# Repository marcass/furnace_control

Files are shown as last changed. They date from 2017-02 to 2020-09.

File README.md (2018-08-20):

# furnace_control
Control a FUWI pellet boiler with arduino to improve smarts

After having 2 controal boards malfunction I have decided to roll my own with some improved modulation of fan speed and pellet feeding. Reporting or interface issues will be addressed also

Goals satisfied with this project are (not limited to):
* Reducing the need for cleaning of pellet boiler through better end of heat cycle managemtn of burner box (basically fanning the pellet wad until it burns out)
* Increasing efficiency of pellet usage by varying energy output of pellet boilder in accordance with demand (pid controlling fan, pellet feed time and pause feed time around setpoint). This has the added benefit of avoiding short-cycling and resultant ash buildup

#Components of system
1. Pellet boiler
2. Sensor network for house (managed by https://github.com/home-climate-control/dz ) - this will pull a pin low on arduino in boiler
3. Arduino controlled PCB in boiler
4. Communicatons server (communicates to arduino via usb-serial port and the rest of the world via MQTT)

This repository deals with the arduino sketch, the PCB and the communication interface on the server

# To perform headless-server update of arduino sketch
1. Stop python listener script on serial port "sudo systemctl stop arduino-attach.service"
2. Upload script to arduino: "make upload" (in root of git repo for furnace_control)
3. Start python listener script on serial port: "sudo systemctl start arduino-attach.service"

## Inputs from boiler
* Water temperature
* Auger shaft temperature
* Light sensor in flame box

## Outputs to boiler and assocaited hardware
* Auger motor to move pellets into flame box
* Fan to stoke fire
* 280W eleement to start fire
* Circ pump to pump heated water to radiators

## Safety
Hardware fail-safes are ideal as software may have problems that result in uncontrolled fire! Currently the boiler uses a device that breaks the neutral feed to the fan and element so it does not provide continuance when it is over a certain termperature (90 degrees C)
 * Error state pulls all relays to low
 * Idle state pulls fan and element to low

## States
1. Idle
2. Start_up
3. Heating
4. Cool_down
5. Error
6. Off

### Idle
 Wait for closed contact from 1-wire bus to transition into start_up. When contact closed: Blow fan to see if flame detected:
* if flame detected -> Heating
* if no flame -> Start_up

### Start up
1. Blow fan first to see if a flame will start
1. Pellet dump to get something for element to light
2. Element heating of pellet load
3. Gentle fan (phase angled to 30% or so) to start fire until light over threshold sensed
4. Pellet feed and full fan when light over threshold
5. Transition into heating when water temp over 50C

### Heating
1. PID control of trend of water temp and this affects fan speed through PWM and pellet feed rate
2. Start circ pump if over 50C
3. Pull fan relay low and circ pump high if temp over 85C
4. Transition to cool down if contact from 1-wire is opened

### Cool_down
1. Pull fan low and circ pump high until temp <60C
2. Transition to idle when below 60C

### Error
 Catch all that pulls fan adn element low

### Off
Don't start the boiler even if dz asks (button press and remote)

##Links
* Triac schematic for fan control (need up to 5A as heat diminishes capability
https://www.circuitar.com/media/product/25/files/Triac_v1.0.pdf

* Phase control for fan:
http://playground.arduino.cc/Main/ACPhaseControl
* ACPWM lib
http://playground.arduino.cc/Code/ACPWM
* Phase control explanation with varying of power output suggestions: http://electronics.stackexchange.com/questions/19273/when-should-i-fire-the-triacs-gate-when-controlling-an-inductive-load-ac-motor

##Connecton notes
* redundant fan_out connection at relay block in case on-board pahse angle not working
* P6 (240v outs) have the hardware thermostat (AB03 90.05) connected in pins 3 and 4 (polarity doesn't matter
  * when below 90C it is closed circuit
  * when above 90C it is open circuit
  * after opening it closes again at 75C
  * this (when closed circuit) supplies 240N to pins 1, 2 and 3 (pump, auger and element)
* 1-wire relay (hobby boards 8 channel) connects at pins 7 and 8 of P1 (low voltage input connector). When it is closed by control software the DZ_pin is pulled to ground
* 15k Ohm resistors need to be rated for 5w on 240VAC side (consumes 3.8W of power)
* 1.5k Resistor needs to be 50W on 240VAC side (consumes 38W of power) if constant power, but as MOC305 datasheet states:

"The power dissapation of this current limiting resistor and the triac driver is very small because the power triac carris the load current as soon as the current through the driver and current limiting resistor reaches the trigger current of teh power triac"

Switching times for the driver are 1 micro second and 4 micro seconds for the power triac

#Setup
Components of the sytsem are:
1. Boiler controller (arduino based on a PCB)
2. Communication interface on serial port
3. Display device(s)

##Boiler controller
PCB in kicad files in this repo
* Could do with 2 additional input pins for sensing hopper level
* Check that 5W resistors are up to the task of phase angle detection

## Communication interface on serial port
Uses:
* pyserial to capture data/print data to serial port (arduino) and insert into database
* paho-mqtt for subscribing/publishing to mosquitto broker
* mosquitto broker for managing infomration

###UDEV
See udev rules in repo:
* On insertion of aruduino usb assign symlink so pyserial can find device
* runs systemd service that starts the pythion script for managing stuff to and from arduino

###Data capture
Inserting data into influxdb and graphing via a vuejs frontend using plotly. See https://skibo.duckdns.org/sensors/#/graphs (repo here: https://github.com/marcass/esp32-sensornet/tree/master/sensornet)

##Device
Any mqtt client that runs on anything will display data from broker
* subscribe to topics:
  * boiler/switch (for turning on/off)
  * boiler/flame (for displaying flame value)
  * boiler/temp/auger
  * boiler/temp/water
  * boiler/temp/setpoint
  * boiler/messages (error messages)
  * boiler/state (state display)

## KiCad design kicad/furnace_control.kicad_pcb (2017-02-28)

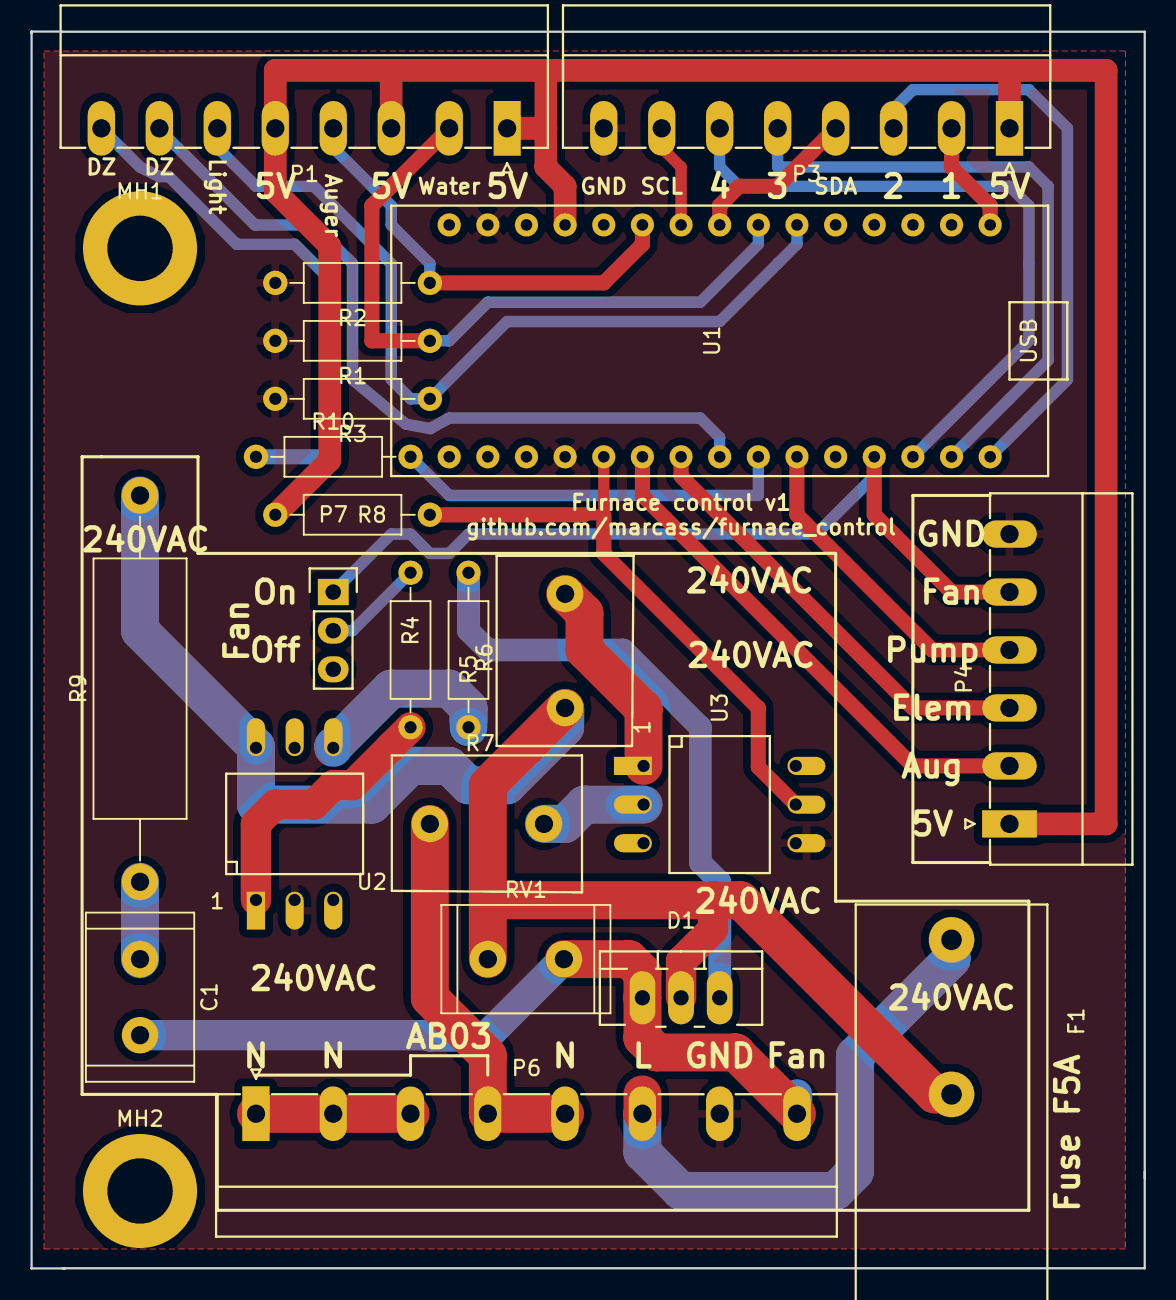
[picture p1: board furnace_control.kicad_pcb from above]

Board: 2 copper layers, 73.2 x 81.3 mm, 24 parts (0 on the bottom side), 31 nets.

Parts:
C1: 0.01muF; R_Radial_Power_L11.0mm_W7.0mm_P5.00mm
D1: Q6015L5; TO-220_Neutral123_Vertical_LargePads
F1: Fuse; Fuseholder5x20_Horizontal_closed_Bulgin_FX0457
MH1, MH2: Mounting_hole; MountingHole_4.3mm_M4_DIN965_Pad
P1: CONN_01X08; PhoenixContact_MC-G_08x3.81mm_Angled
P3: LCD_Button; PhoenixContact_MC-G_08x3.81mm_Angled
P4: CONN_01X06; PhoenixContact_MC-G_06x3.81mm_Angled
P6: 240_CONN_Therm_on_3_4; PhoenixContact_MC-G_08x5.08mm_Angled
P7: Jumper; Pin_Header_Straight_1x03
R1, R2, R3, R8: 10k; R_Axial_DIN0207_L6.3mm_D2.5mm_P10.16mm_Horizontal
R4, R10: 220; R_Axial_DIN0207_L6.3mm_D2.5mm_P10.16mm_Horizontal
R5: 1.5k; R_Axial_DIN0207_L6.3mm_D2.5mm_P10.16mm_Horizontal
R6, R7: 15K; Resistor_5W_l12.5_w9_P7.5
R9: 33; R_Axial_DIN0617_L17.0mm_D6.0mm_P25.40mm_Horizontal
RV1: Varistor 600V; R_Radial_Power_L11.0mm_W7.0mm_P5.00mm
U1: arduino_nano; ArduinoNano
U2: MOC3052M; Optocoupler_6pin_wide_Stile-I
U3: H11AA1; Optocoupler_6pin_wide_Stile-I

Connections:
+5V: P1.1, P1.3, P1.5, P3.1, P4.1, R8.1, U1.12
/N: P6.1, P6.2, P6.3
/Neutral: P6.4, P6.5, R7.1
Button_1: P3.2, U1.1
Button_2: P3.3, U1.30
Button_3: P3.5, U1.29
Button_4: P3.6, U1.28
GND: P3.8, P4.6, P6.7, R1.2, R2.2, R3.2, U1.14, U1.19, U2.2, U3.4
unnamed: C1.1, R9.1
unnamed: C1.2, D1.1, P6.8, RV1.2
unnamed: D1.2, F1.2, R6.1, R9.2, RV1.1, U2.6
unnamed: D1.3, R5.1
unnamed: F1.1, P6.6
unnamed: P1.8, R10.1
unnamed: P7.2, R4.2
unnamed: R4.1, U2.1
unnamed: R5.2, U2.4
unnamed: R6.2, U3.1
unnamed: R7.2, U3.2
Out_auger: P4.2, U1.21
SCL: P3.7, U1.9
SDA: P3.4, U1.8
ac_in: R8.2, U1.20, U3.5
auger_temp: P1.4, R2.1, U1.10
dz_pin: P1.7, U1.23
dz_supply: R10.2, U1.24
element: P4.3, U1.22
fan_out: P4.5, P7.1, U1.27
light: P1.6, R3.1, U1.6
pump: P4.4, U1.25
water_temp: P1.2, R1.1, U1.7

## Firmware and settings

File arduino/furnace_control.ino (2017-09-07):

/* ToDo
 *  - check lcd working
 *  - put ultrasound probe on analoge pins (as digital?)
 */

/*******************************
 BOILER CONTROL
 *******************************/
//#define debug
#define pid //use if PID controlling fan output
//#define no_PID //use if not pid controlling
#define mqtt
//#define ac_counter
//#define lcd //interferes with interrupts?

//Libraries
//#include <Wire.h>
//#ifdef lcd
//  //https://bitbucket.org/fmalpartida/new-liquidcrystal/wiki/Home
//  #include <LiquidCrystal_I2C.h>
//  LiquidCrystal_I2C lcd(0x27, 2, 1, 0, 4, 5, 6, 7, 3, POSITIVE);  // Set the LCD I2C address
////need to set contrast and backlight and check pin assignments
//#endif
//PID library
#include <math.h>
#include <PID_v1.h>
//for ac phase angle stuff
#include <avr/io.h>
#include <avr/interrupt.h>
#include "FastRunningMedian.h" //for getting flame val median http://forum.arduino.cc/index.php?topic=53081.msg1160999#msg1160999

/*******************************************************************************
 * Constants
 */
//timers
unsigned long ELEMENT_TIME = 450000; //7.5min in ms
unsigned long START_FEED_TIME = 120000; //2min in ms for pellet feed initially
unsigned long SUBSEQUENT_START_FEED_TIME = 5000; //little top up of pellets if not starting first time
unsigned long START_FAN_TIME = 120000; //2min in ms for time to blow to see if flame present
//const long DUMP_START = 45000;//45s of fanning before throwing a little fuel on the fire
unsigned long END_FAN_TIME = 600000; //10min of blow to empty puck from burn box
unsigned long PUMP_TIME = 30000; //30s in ms to avoid short cycling pump
unsigned int BUTTON_ON_THRESHOLD = 1500;//1.5s in ms for turning from off to idle and vice versa
unsigned long FEED_PAUSE = 24000; //60s and calculating a result so might need to be a float
unsigned long FEED_TIME = 10000;//default pellet feed time
unsigned long STATE_CHANGE_THRES = 5000;//time that needs to elapse before changing STATE_START_UP <- STATE_HEATING
unsigned long STATE_CHANGE_THRES_UP = 2000;//time that needs to elapse before changing STATE_START_UP -> STATE_HEATING
unsigned long STOP_THRESH = 5000; //for  fan short cycling
unsigned long ERROR_THRES = 5000;//time that must elapse before goes into error at startup (not working at present)
unsigned long RESET_THRESHOLD = 300000; //time that must elapse before start count gets reset
unsigned int FLAME_READ_INTERVAL = 30; //read flame val every 30ms to build array for calculating average value (smoothing)
//temps
const int LOW_TEMP = 50; //deg C -> low end of heating range
const int HIGH_TEMP = 75; //deg C -> high end of heating range
const int MID_TEMP = 63;//Send back to heating if over heats from here
const int TOO_HOT_TEMP = 85; //cool down NOW
const int AUGER_OVER_TEMP = 45; //deg C - don't want a hopper fire
//flame values
const int FLAME_VAL_THRESHOLD = 120;//work out a value here that is reasonable
const int START_FLAME = 50;
//States
const int STATE_IDLE = 0;
const int STATE_START_UP = 1;
const int STATE_HEATING = 2;
const int STATE_COOL_DOWN = 3;
const int STATE_ERROR = 4;
const int STATE_OFF = 5;
//Buttons (numbers from left
const int BUTTON_1 = 13;
const int BUTTON_2 = 12;
const int BUTTON_3 = 11;
const int BUTTON_4 = 10;
//Outputs
const int PUMP = 7; //circ pump relay
const int FAN = 9; //fan relay. pin9 is a PWM pin and allows for analogWrite
const int AUGER = 3; //pellet auger relay
const int ELEMENT = 4; //fire starting element relay
//Inputs
const int WATER_TEMP = 3; //analogue pin 3
const int AUGER_TEMP = 6; //analogue pin 6
const int LIGHT = 2; //analogue pin 2 for flame detection
const int DZ_PIN = 5; // pin that is pulled up when 1-wire relay closes
const int DZ_SUPPLY = 6; //Need a pin to supply 5v that is passed to DZ_PIN when 1-wire relay closes
#define DETECT 2 //ac detection pin
#define GATE 9 //pwm pin
#define PULSE 4   //trigger pulse width (counts) that triac requires to fire one specified needs ~25mus

/********************************************************************************************
 * Variables
 */ 
// general timers (specific ones in subsection)
unsigned long debounce_start = 0; //button press debounce
unsigned long element_start = 0;
unsigned long fan_start = 0;
unsigned long fanend_start = 0;
unsigned long auger_start = 0;
unsigned long reset_dump_count;
unsigned long state_trans_start = 0;
unsigned long state_trans_stop = 0;
unsigned long stop_start = 0; //for  fan short cycling
unsigned long start_feed_time = 0;//pellets
unsigned long start_feed_pause = 0;//pellets
unsigned long start_pump_time = 0;//pump short cycling
int on_wait; //variable for converting power to timer value
unsigned long feed_pause;//var for pellets puase time
unsigned long feed_time;//var for feed time
//sensor readings
int auger_temp;
int flame_val; // range from 0 to 1024 ( i think)
//counters
int start_count = 0;
int crosses;
int counts;
int dump_count = 0;//counter to make sure we don't fill up chamber with pellets
//tests
bool reset = false;
bool feeding = true;
bool cooling = false;
bool dump = false;
bool elem = false;
bool blowing = false;
//maths
int proportion;
float divisor;
//state stuff
String reason = "";
int state;
int this_state;
//reading flame value stuff and smoothing
FastRunningMedian<int, 32, 1> newMedian;
// Constructor: 
// FastRunningMedian<datatype_of_content, size_of_sliding_window, default_value> 
// maximim size_of_sliding_window is 255
// Methods:
// addValue(val) adds a new value to the buffers (and kicks the oldest)
// getMedian() returns the current median value
unsigned long prevMillis;
//const int numReadings = 10;
//int readings[numReadings];      // the readings from the light sensor
//int readIndex = 0;              // the index of the current reading
//int total = 0;

/****************************************************************************************
 * PID
 */
#ifdef pid
  double Kp=10, Ki=0.001, Kd=1; //P, I and D see http://playground.arduino.cc/Code/PIDLibrarySetTunings
  double temp_set_point = 63; //PID temp SETPOINT
  double power; //variable for percentage power we want fan to run at works from 30 (min) to 80 (max)
  double water_temp;
  double feed_pause_percent;
  double feed_percent;
  //PID fanPID(&Input, &Output, &Setpoint,2,5,1, DIRECT);
  PID fanPID(&water_temp, &power, &temp_set_point,Kp, Ki, Kd, DIRECT); //need more fan power to get hotter so DIRECT
  PID pausePID(&water_temp, &feed_pause_percent, &temp_set_point,Kp, Ki, Kd, REVERSE); //need shorter feed time to get to hotter so REVERSE
  PID feedPID(&water_temp, &feed_percent, &temp_set_point,Kp, Ki, Kd, DIRECT);
  /* maths  may need to be addedfor value calcs (pid outputs value of 0-255 and we want to convert to 
   *  range in percentage limits
   *  http://playground.arduino.cc/Code/PIDLibrarySetOutputLimits states that 
   *  feedPID.SetOutputLimits(40,100); should alter default behavior, but I wonder if it is a trncater version
   *  of 0-255
   *  - fan runs at 30-80% of power (phase angle control fails outside that range)
   *  - pellets feed I want to run at 40-100% of time in range
   *  - pause I want to run between 60-100% of time in range
   */
#endif

#ifdef no_PID
  int power; //variable for percentage power we want fan to run at works from 30 (min) to 80 (max)
  int water_temp; 
#endif

//MQTT *****************************************************************************************

#ifdef mqtt
  long PUB_INTERVAL = 1000; //1 second to cylce between publishing events while running
  long previousMillis = 0;
  const long PUB_INTERVAL_IDLE = 30000; //publish state info and temp info for logging while not running
  int index = 0; //counter for cycling through publishing array
  //topics
  int fan_power; //what fan is actually running at
  String STATE_TOPIC = "boiler/state";
  String WATER_TEMP_TOPIC = "boiler/temp/water";
  String AUGER_TEMP_TOPIC = "boiler/temp/auger";
  String FLAME_TOPIC = "boiler/flame";
  String ERROR_TOPIC = "boiler/messages";
  String PID_FAN = "boiler/pid/fan";
  String PID_FEED = "boiler/pid/feed";
  String PID_PAUSE = "boiler/pid/pause";
  String START_COUNT_TOP = "boiler/start_count";
  String TEMP_SET_POINT_TOP = "boiler/temp/setpoint";
  const String STATES_STRING[] = {"Idle","Starting","Heating","Cool down","Error","Off","Wind down"};
  
  //publish functions overloaded for int/string as payload
  void publish(String top,int payload) { //publish data
    Serial.print("MQTT:");
    Serial.print(top);
    Serial.print("/");
    Serial.println(payload);
  }
  void publish(String top,String payload) { //publish data
    Serial.print("MQTT:");
    Serial.print(top);
    Serial.print("/");
    Serial.println(payload);
  } 
#endif

// SETUP SERIAL COMM for inputs *********************************************************
String inputString = "";         // a string to hold incoming data
boolean stringComplete = false;  // whether the string is complete

void serialEvent() {
  while (Serial.available()) {
    // get the new byte:
    char inChar = (char)Serial.read();  // add it to the inputString:
    inputString += inChar;
    if (inChar == '\n') {
      stringComplete = true;
    } 
  }
}

//phase angle interrupts ***************************************************************
void zeroCrossingInterrupt(){ //zero cross detect   
  TCCR1B=0x04; //start timer with divide by 256 input
  TCNT1 = 0;   //reset timer - count from zero
  crosses++;
}

ISR(TIMER1_COMPA_vect){ //comparator match
  digitalWrite(GATE,HIGH);  //set TRIAC gate to high
  TCNT1 = 65536-PULSE;      //trigger pulse width
}

ISR(TIMER1_OVF_vect){ //timer1 overflow
  digitalWrite(GATE,LOW); //turn off TRIAC gate
  TCCR1B = 0x00;          //disable timer stopd unintended triggers
}

//Analogue reading maths for temp ******************************************************
double Thermistor(int RawADC) {
 double Temp;
 Temp = log(10000.0*((1024.0/RawADC-1)));
 //         =log(10000.0/(1024.0/RawADC-1)) // for pull-up configuration
 Temp = 1 / (0.001129148 + (0.000234125 + (0.0000000876741 * Temp * Temp ))* Temp );
 Temp = Temp - 273.15;            // Convert Kelvin to Celcius
 //Temp = (Temp * 9.0)/ 5.0 + 32.0; // Convert Celcius to Fahrenheit
 return Temp;
}


void setup() {
  //intitialise output pins (inputs are all analogue read pins)
  pinMode(DETECT, INPUT);     //zero cross detect
  digitalWrite(DETECT, HIGH); //enable pull-up resistor
  pinMode(GATE, OUTPUT);      //TRIAC gate control
  digitalWrite(GATE, LOW);
  pinMode(PUMP, OUTPUT);
  digitalWrite(PUMP, LOW);
  pinMode(FAN, OUTPUT);
  digitalWrite(FAN, LOW);
  pinMode(AUGER, OUTPUT);
  digitalWrite(AUGER, LOW);
  pinMode(ELEMENT, OUTPUT);
  digitalWrite(ELEMENT, LOW);
  pinMode(DZ_SUPPLY, OUTPUT);
  digitalWrite(DZ_SUPPLY, LOW);
  //digitalWrite(A2, LOW);
  //Initialise inputs
  pinMode(DZ_PIN, INPUT_PULLUP);
  pinMode(BUTTON_1, INPUT_PULLUP);
  pinMode(BUTTON_2, INPUT_PULLUP);
  pinMode(BUTTON_3, INPUT_PULLUP);
  pinMode(BUTTON_4, INPUT_PULLUP);
  #ifdef pid
    //initialize the PID variables we're linked to
    fanPID.SetOutputLimits(30, 80); //percentage of fan power
    fanPID.SetSampleTime(3000); //SAMPLES EVERY 3s
    pausePID.SetOutputLimits(100, 170); //percentage of feed time check to see that burning all of load
    pausePID.SetSampleTime(3000);
    feedPID.SetOutputLimits(60,100); //percentage of feed time check to see that burning all of load
    feedPID.SetSampleTime(3000);
    //turn the PID on
    fanPID.SetMode(AUTOMATIC);
    pausePID.SetMode(AUTOMATIC);
    feedPID.SetMode(AUTOMATIC);
  #endif
  // set up Timer1 
  //(see ATMEGA 328 data sheet pg 134 for more details)
  OCR1A = 100;      //initialize the comparator
  TIMSK1 = 0x03;    //enable comparator A and overflow interrupts
  TCCR1A = 0x00;    //timer control registers set for
  TCCR1B = 0x00;    //normal operation, timer disabled
  // set up zero crossing interrupt
  attachInterrupt(0,zeroCrossingInterrupt, RISING); //IRQ0 is pin 2. Call zeroCrossingInterrupt 
  // initialize serial communication:
  Serial.begin(9600);//slower speed for long cable
  inputString.reserve(200); // reserve mem for received message on serial port 
  int state = 0;
  #ifdef mqtt
    //initialise state as idle on statup
    Serial.print("MQTT:");
    Serial.print(STATE_TOPIC);
    Serial.print("/");
    Serial.println(STATES_STRING[state]);
  #endif
}

//Functions that do stuff ********************************************************************
void fan(bool runFan, int x) {
  #ifdef mqtt
    fan_power = x;
  #endif
  if (!runFan) {
    digitalWrite(GATE,LOW);
    //undo phase angle magic here 
    TCCR1B = 0x00;
    TIMSK1 = 0x00;    //disable comparator A and overflow interrupts
    TCCR1A = 0x00;    //timer control registers set for
    TCCR1B = 0x00;    //normal operation, timer disabled
    stop_start = 0;
    power = 0;
  }
  if (runFan) {
    #ifdef debug
      Serial.print(" FAN ON at ");
      Serial.print(x);
    #endif
    if (x == 100) { //no phase angle control needed if you want balls out fan speed
      digitalWrite(GATE,HIGH);
    }else {
      //do magic phase angle stuff here
      /* x is the int as a percentage of fan power
       * OCR1A is the comparator for the phase angle cut-off
       * - when TCNT1 > OCR1A, ISR(TIMER1_OVF_vect) is called tellng optocoupler to power down
       * - 520 counts (16000000 cycles scaled to 256) per half AC sine wave @60hz (i think we run at 50Hz)
       * - fan stops over 80% of power, presumably latching the triac confusion over next zero cross => less than 156 count delay
       * - 30% is the lower power limit to avoid firing the triac too close to teh zero cross => delay not more than 364 count delay
       * - The smaller the value of OCR1A the more power we have
       */
      TIMSK1 = 0x03;    //enable comparator A and overflow interrupts
      //set up interrupt
      
      //attachInterrupt(0,zeroCrossingInterrupt, RISING);  // inturrupt 0 on digital pin 2
      
      //set a value that is a proportion of 520 for power
      divisor = (float)x / 100;
      proportion = divisor * 520;
      on_wait = 520 - proportion;
      if ( on_wait < 104) {
        OCR1A = 104;
      }
      if ( on_wait > 364) {
        OCR1A = 364;
      }else {
        OCR1A = on_wait;
      }
    }
  }
}

void pump(bool on) { //prevents short cycling of pump
  #ifdef debug
    Serial.print(" Pump: ");
    Serial.print(on);
  #endif 
  if (on) {
    digitalWrite(PUMP, HIGH);
    if (start_pump_time == 0) {    //avoid short cycling so pump for at least 30s
      start_pump_time = millis();
    }
  }
  if (!on) {
    if ( (millis() - start_pump_time) > PUMP_TIME) {
      digitalWrite(PUMP, LOW);
      start_pump_time = 0;
    }
  }
}

void flame_value_median() {
  unsigned long currentMillis = millis();
  if(currentMillis - prevMillis > FLAME_READ_INTERVAL) { 
    prevMillis = currentMillis; 
    newMedian.addValue(analogRead(LIGHT));
    flame_val = newMedian.getMedian();
  }
}


void fan_and_pellet_management() {
  //water temp measured in safety()
  //FAN MANAGEMENT
  if (water_temp < LOW_TEMP) { //go hard on the fan
    fan(true, 100);
  }else if (water_temp > HIGH_TEMP) {
    this_state = STATE_HEATING;
    state = STATE_COOL_DOWN;
    #ifdef mqtt
      //
      publish(STATE_TOPIC, STATES_STRING[state]);
    #endif    
  }else {
    #ifdef no_PID
      power = 75; //arbitrary value
    #endif
    fan(true, (int)power);
  }
  //PELLETS MANAGEMENT
  #ifdef pid
    feed_pause = (feed_pause_percent / 100) * FEED_PAUSE; //caluclate actual pause from PID derived value
    feed_time =  (feed_percent / 100)       * FEED_TIME;
  #endif
  #ifdef no_PID //won't be changing so set to const int value
    feed_time = FEED_TIME;
    feed_pause = FEED_PAUSE;
  #endif
  if (feeding) {
    if (start_feed_time == 0) {
      start_feed_time = millis();
    }
    //test to see if feed been on for long enough
    if ( (millis() - start_feed_time) > feed_time) {
      //stop feeding and start pausing
      feeding = false;
      start_feed_time = 0;
      //start_feed_pause = millis();
      digitalWrite(AUGER, LOW);
      #ifdef debug
        Serial.print("  Auger off  ");
      #endif
    }else {
      digitalWrite(AUGER, HIGH);
      #ifdef debug
        Serial.print("  Auger on  ");
      #endif 
    }
  } 
  if (!feeding) { 
    if (start_feed_pause == 0 ) {
      start_feed_pause = millis();
    }
    if ( (millis() - start_feed_pause) > feed_pause) {
      //stop pausing, start feeding
      
      start_feed_pause = 0;
      feeding = true;
    }
  }
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
void loop() {
  #ifdef debug
    Serial.print(" Sensors: ");
    Serial.print("W = ");
    Serial.print(water_temp);
    Serial.print(" A = ");
    Serial.print(auger_temp);
    Serial.print(" F = ");
    Serial.print(flame_val);
    Serial.print("State = ");
    Serial.println(STATES_STRING[state]);
  #endif 
  //***************   safety  *********************
  safety();
  //*************  see if we need to turn on or off  **************
  //get flame_val average
  flame_value_median();
  //dz calls it: 1-wire relay gets closed by DZ3
  if (digitalRead(DZ_PIN) == HIGH) {
    if ((state == STATE_HEATING) || (state == STATE_START_UP)) {
      fanend_start = 0;//not going for end fan time so trying to reset variable here
      this_state = STATE_IDLE;
      state = STATE_COOL_DOWN;
      #ifdef mqtt
        //
        publish(STATE_TOPIC, STATES_STRING[state]);
      #endif  
    }
  }
  //button press?
//  if (digitalRead(BUTTON_1) == HIGH) {
//    if (debounce_start == 0) {
//      debounce_start = millis();
//    }
//    if ( (millis() - debounce_start) > BUTTON_ON_THRESHOLD) {
//      if (state != STATE_OFF) {
//        state = STATE_IDLE;
//        #ifdef mqtt
//          //
//          publish(STATE_TOPIC, STATES_STRING[state]);
//        #endif        
//      }else {
//        state = STATE_OFF;
//        #ifdef mqtt
//          //
//          publish(STATE_TOPIC, STATES_STRING[state]);
//        #endif        
//      }
//      debounce_start = 0;
//    }else if (digitalRead(BUTTON_1) == LOW) { //button not held long enough so don't turn switch state and reset counter
//      debounce_start = 0;
//    }
//  }
  //serial instruction
  if (stringComplete) {
    if (inputString.startsWith("Turn Off Boiler")) {
      inputString = "";
      //reason = "";
      stringComplete = false;
      if ((state == STATE_IDLE) or (state == STATE_OFF) or (state == STATE_ERROR)){
        state = STATE_OFF;
      }else{
        this_state = STATE_OFF;
        state = STATE_COOL_DOWN;
      }
      #ifdef mqtt
        publish(STATE_TOPIC, STATES_STRING[state]);
      #endif
    }
    if (inputString.startsWith("Turn On Boiler")) {
      inputString = "";
      stringComplete = false;
      state = STATE_IDLE;
      #ifdef mqtt
        publish(STATE_TOPIC, STATES_STRING[state]);
      #endif
//      reason = "";
//      #ifdef mqtt
//        //
//        publish(ERROR_TOPIC, reason); //clear error register
//      #endif    
      start_count = 0;  
      //delay(10);
    }else if (inputString.startsWith("Increase SetPoint")) {
      inputString = "";
      stringComplete = false;
      if (temp_set_point < 73){
      (int)temp_set_point++; 
      publish(TEMP_SET_POINT_TOP, temp_set_point);     
      }
      

    }else if (inputString.startsWith("Decrease SetPoint")) {
      inputString = "";
      stringComplete = false;
      if (temp_set_point > 60){
        (int)temp_set_point--;
        publish(TEMP_SET_POINT_TOP, temp_set_point);
      }
      
    }
  }
  
  switch (state) {
    case STATE_IDLE:
      proc_idle();
      break;
    case STATE_START_UP:
      proc_start_up();
      break;
    case STATE_HEATING:
      proc_heating();
      break;
    case STATE_COOL_DOWN:
      proc_cool_down(this_state);
      break;
    case STATE_ERROR:
      proc_error();
      break;
     case STATE_OFF:
      proc_off();
      break;
  }
  if (stringComplete){
    inputString = "";
    stringComplete = false;
  }
  #ifdef mqtt
    if ((state == STATE_START_UP) or (state == STATE_HEATING) or (state == STATE_COOL_DOWN)) { //publishs
      int mosqPayload[] = {water_temp, auger_temp, flame_val, state, fan_power, feed_percent, feed_pause_percent, temp_set_point};
      const String mosqTop[] = {WATER_TEMP_TOPIC, AUGER_TEMP_TOPIC, FLAME_TOPIC, STATE_TOPIC, PID_FAN, PID_FEED, PID_PAUSE, TEMP_SET_POINT_TOP};
      //publish everything in a round robin fashion
      if(millis() - previousMillis > PUB_INTERVAL) { //publish info
        previousMillis = millis();  
        if (index < 7 ) {
          index++; 
        }else {
          index = 0;
        }
        if (index==3){
         publish(mosqTop[index], STATES_STRING[state]);
        }else{
          publish(mosqTop[index], mosqPayload[index]);
        }
      }
    }else { //publish temp, pause for PUB_INTERVAL_IDLE, publish state, pause for PUB_INTERVAL_IDLE, publish temp etc
      if (index > 1) {//set it to value for publishing if was in higher value from prev on state
        index = 0;
      }
      if( (millis() - previousMillis) > PUB_INTERVAL_IDLE) { //publish info
        previousMillis = millis();
        if (index < 1) { 
          publish(WATER_TEMP_TOPIC, water_temp);//water temp in first member of arrays
          index++;
        }
        if (index == 1) {
          publish(STATE_TOPIC, STATES_STRING[state]);
//          if (state == STATE_ERROR) {
//            publish(ERROR_TOPIC, reason);
//          }
          index = 0;
        }
      }
        
    }

  #endif
  #ifdef ac_counter
    if (crosses > 60) {
      crosses = 0;
      counts++;
      Serial.print("Number of counts = ");
      Serial.println(counts);
    }
  #endif
  //delay(200); //can't read form serial with delay
}

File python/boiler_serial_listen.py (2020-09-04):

import serial
import time
# import boiler_alerts as alerts
import creds
import paho.mqtt.client as mqtt
import paho.mqtt.publish as publish
import requests
import creds
import json
from threading import Thread

AUTH_URL = 'https://skibo.duckdns.org/api/auth/login'
DATA_URL = 'https://skibo.duckdns.org/api/data'
headers = ''
jwt = ''

# dict of topics for messaging
boiler_topics = {"boiler/state":"State", "boiler/temp/water":"Water temp", "boiler/temp/auger": "Auger temp", "boiler/temp/setpoint": "Setpoint"}
boiler_data = {'State': '', 'Water temp': 0, 'Auger temp': 0, 'Setpoint': 0}
state_arr = ['Idle', 'Starting', 'Heating', 'Cooling', 'Error', 'Off']

def getToken():
    global jwt
    global headers
    r = requests.post(AUTH_URL, json = {'username': creds.user, 'password': creds.password})
    tokens = r.json()
    #print 'token data is: ' +str(tokens)
    try:
        jwt = tokens['access_token']
        headers = {"Authorization":"Bearer %s" %jwt}
    except:
        print ('oops, no token for you')

def post_data(data):
    global jwt
    global headers
    if (jwt == ''):
        print ('Getting token')
        getToken()
    ret = requests.post(DATA_URL, json = data, headers = headers)
    #print 'JWT = '+str(jwt)
    #print 'First response is: ' +str(ret)
    if '200' not in str(ret):
        print ('Oops, not authenticated')
        try:
            getToken()
            requests.post(DATA_URL, json = data, headers = headersi)
            ret = {'Status': 'Error', 'Message': 'Got token'}
            print ('Post NOT 200 response is: ' +str(r))
        except:
            ret =  {'Status': 'Error', 'Message': 'Failed ot get token, so cannot perform request'}
    #print ret
    #return ret.json()

# The callback for when the client receives a CONNACK response from the server.
def on_connect(client, userdata, flags, rc):
    print("Connected with result code "+str(rc))
    # Subscribing in on_connect() means that if we lose the connection and
    # reconnect then subscriptions will be renewed.
    client.subscribe("boiler/#")

# The callback for when a PUBLISH message is received from the server.
def on_message(client, userdata, msg):
    message = str(msg.payload, 'UTF-8')
    if 'switch' in msg.topic:
        #print ("port write request received")
        #print(message)
        if ('Setpoint' in message) or ('State'  in message):
            port.write('\r\n'+message+'\r')
            print ('Sent ' + message + ' to serial port.')
    allowed_passthrough_msg = ['Turn Off Boiler', 'Turn On Boiler', 'Increase SetPoint', 'Decrease SetPoint']
    if message in allowed_passthrough_msg:
        #print ("Message allowed through")
        to_send = ('\r\n'+message+'\r\n').encode()
        port.write(to_send)
        #port.write(('\r\n'+message+'\n\r').encode())
        #port.write('\r\n')
        #port.write(message)
        #port.write('\r')
        #print ('Sent ' + message + ' to serial port.')

def parse_packet(payload, sensor):
    #payload = str(payload, 'UTF-8')
    #print(sensor, payload)
    try:
        if 'temp' in sensor:
            temp_type = sensor.split('/')[-1:][0]
            #print ('temp type is: '+str(temp_type)+', value is: '+payload)
            #data.write_data(temp_type, 'temperature', int(payload))
            packet = {'tags': {'state':boiler_data['State'], 'type':'temp', 'sensorID':temp_type, 'site': 'boiler'}, 'value':float(payload), 'measurement': 'things'}
        if 'state' in sensor:
            state = int(payload)
            # Publish string value to state
            readable_state = state_arr[state]
            boiler_data['State'] = readable_state
            client.publish('boiler/state/readable/', readable_state, 0, True)
            packet = {'tags': {'state':boiler_data['State'], 'type':'state', 'sensorID':'state', 'site': 'boiler'}, 'value':state, 'measurement': 'things'}
        if 'pid' in sensor:
            pid_type = sensor.split('/')[-1:][0]
            pids = ['fan', 'pause', 'feed']
            if pid_type in pids:
                # data.write_data(pid_type, 'pid', int(payload))
                packet = {'tags': {'state':boiler_data['State'], 'type':'pid', 'sensorID':pid_type, 'site': 'boiler'}, 'value':int(payload), 'measurement': 'things'}
            else:
                print('Mangled PID typ')
        if 'flame' in sensor:
            # data.write_data('burn', 'flame', int(payload))
            packet = {'tags': {'state':boiler_data['State'], 'type':'light', 'sensorID':'flame', 'site': 'boiler'}, 'value':int(payload), 'measurement': 'things'}
        #print(packet)
        return packet
    except:
        packet = 0
        return packet


def write_setpoint(setpoint):
    port.write('\r\n'+'Setpoint'+'['+setpoint+']'+'\r')
    print ('Sent Setpoint[' + setpoint + '] to serial port.')

def write_state(state):
    # "Idle","Starting","Heating","Cool down","Error","Off"
    port.write('\r\n'+'State'+'['+state+']'+'\r')
    print ('Sent State[' + state + '] to serial port.')

def readlineCR(port):
    global boiler_data
    global client
    rv = ""
    while True:
        ch = port.read()
#        print(ch)
#        rv += ch
#       for python3 need to cast to str
        try:
            rv += str(ch, 'UTF-8')
        except:
            print('Serial character decoding error')
            pass
#        rv += str(ch)
#        print(rv)
        if ch==b'\r':# or ch=='':
            print(rv)
            try:
                if 'boiler' in rv:
                    #received = rv
                    received = rv[:-1]
                    #print("rec = "+str(received))
                    payload = received.split('^')
                    #sensor = payload[0][1:]
                    sensor = payload[0]
                    #print(payload, sensor)
                    #sensor_arr = sensor.split('/')
                    value = payload[1]
                    try:
                        packet = parse_packet(value, sensor)
                        client.publish('hcc/boiler/', str(packet), 0, True)
                    except:
                        print('Could not parse packet, skipping')
                        pass
            except:
                print('Serial garbage. Discarding')
                pass
            return rv
        else:
            #do nothing
            dumb_var = 1
            #print('keep building')


# Alerts setup:
# def chat_messg(msg):
#     if '/turn off' in msg['text']:
#         print ('turning off')
#         port.write('\r\n'+'Turn Off Boiler'+'\r')
#         return
#     if '/turn on' in msg['text']:
#         print ('turning on')
#         port.write('\r\n'+'Turn On Boiler'+'\r')
#         return
#     else:
#         print ('doing other stuff')
#         alerts.on_chat_message(msg, boiler_data)
#         return
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

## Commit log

2017-02-15 Code update for arduino
2017-02-15 Added sketch for reading analogue sensors
2017-02-15 Added internal pullup to switching
2017-02-15 Added kicad files
    [furnace_control.kicad_pcb, furnace_control.sch]
2017-02-15 updated for phase angle control and schematic
    [furnace_control.sch]
2017-02-16 pcb started
    [furnace_control.kicad_pcb, furnace_control.sch]
2017-02-16 updated and checked PCB
    [furnace_control.kicad_pcb, furnace_control.sch]
2017-02-16 Updated README and notes on shcematic for power ratings of resistors
    [furnace_control.sch]
2017-02-16 updatred schematic
    [furnace_control.sch]
2017-02-17 updated schematic for parts ordered
    [furnace_control.sch]
2017-02-17 Added temperature readings to sketch and updated readme with power stuff
    [furnace_control.sch]
2017-02-17 udated pcb for fuse
    [furnace_control.kicad_pcb, furnace_control.sch]
2017-02-18 Added poser resitors to board
    [furnace_control.kicad_pcb, furnace_control.sch]
2017-02-21 updated sketch in prep for PID control
2017-02-28 sorted out light reading fuck up
    [furnace_control.kicad_pcb]
2017-02-28 updated fan test stuff
2017-02-28 updated pcb
    [furnace_control.kicad_pcb]
2017-03-01 set up pid variables
2017-03-01 added pid test
2017-03-01 tested pid tests and modified code
2017-03-02 still need to sort fan
2017-03-02 hopefully sorted fan
2017-03-02 fan not sorted in start up
2017-03-02 fixed fan now?
2017-03-03 rationalised fan management
2017-03-03 fan fixed
2017-03-03 loop for sensors with delay inbetween
    [furnace_control.sch]
2017-03-03 fan not fixed
2017-03-03 pump test
2017-03-03 pid problems sorted?
2017-03-05 reset start_count on turning from STATEOFF to STATE_ON
    [furnace_control.ino]
2017-03-05 fiddled with pid tunings
2017-03-07 fixed fan not stopping on cool down
    [furnace_control.ino]
2017-03-08 fixed logic error. this time??
    [furnace_control.ino]
2017-03-08 strapped on fix for cool down
    [furnace_control.ino]
2017-03-12 chnaged fan fucntion
2017-03-12 more fan sorting
2017-03-13 changing pid settings
2017-03-23 increased element time and dump, began dump_count reset logic
    [furnace_control.ino]
2017-05-08 updated switching of boiler to off and put limits on set point
2017-05-29 Increase final fan blow time to get rid of more ash
2017-07-04 more timer fiddling
2017-07-06 more timeing issues at fan end
    [furnace_control.ino]
2017-09-05 fixed trans to state_off when in idle
    [furnace_control.ino]
2018-08-16 boiler as a sensor
2018-08-19 not publishing temp, fixed?
    [boiler_serial_listen.py]
2018-08-20 resolved failiure of script
    [boiler_serial_listen.py]
2018-10-02 update fan test for new fan
2018-10-03 new fan in commision
2020-08-18 prints for debugging
2020-08-27 filterd pid types
